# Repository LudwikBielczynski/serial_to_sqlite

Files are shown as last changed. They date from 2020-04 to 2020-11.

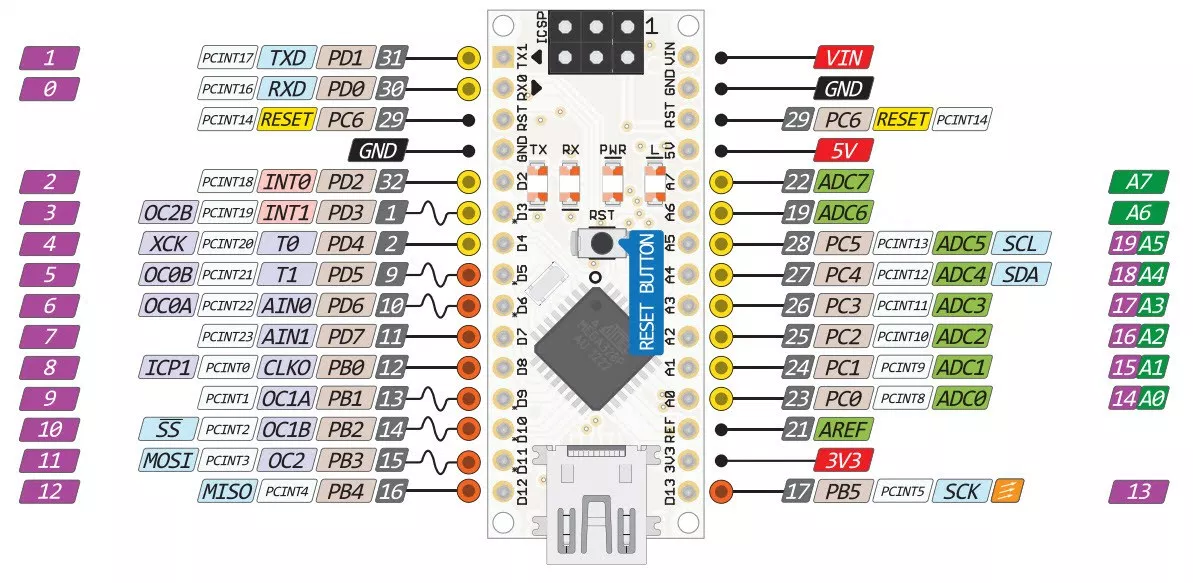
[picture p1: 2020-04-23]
schemes/arduino_nano_pin_layout.jpg

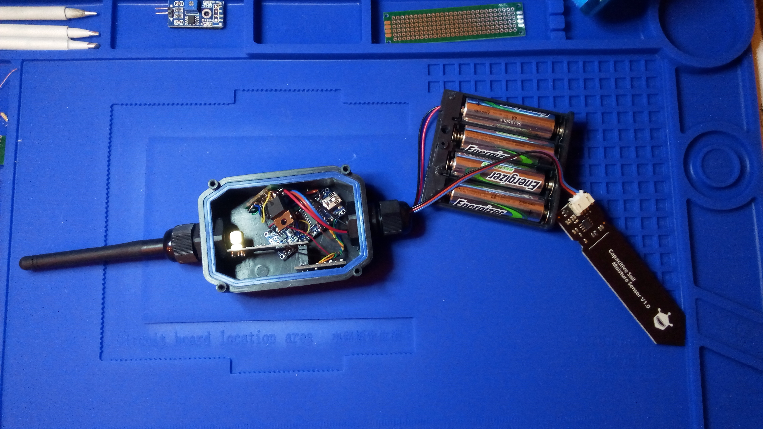
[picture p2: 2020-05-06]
prototypes/2020-05-06_soil_humidity_module.jpg

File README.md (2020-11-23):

# General scheme
General scheme of the watering control system is shown below:


Code to program transmitter and receiver arduino microcontrollers are available in sensors directory.

# Wiring schemes
## Receiver module
The wiring scheme for the receiver module is as follows:


## Soil humidity module
When compared with the receiver module, the wiring scheme of the soil humidity module has additionally (i) an external power supply, (ii) a voltage divider plugged to the analog pin (to measure the voltage of the battery), and (iii) the soil humidity sensor.


<!-- A prototype is shown below:
![alt text](https://github.com/LudwikBielczynski/watering_control_system/blob/master/prototypes/2020-05-06_soil_humidity_module.jpg) -->

# Receiver module
## Install as a service
The sensor_listener.service script should be placed in the /etc/systemd/system folder.

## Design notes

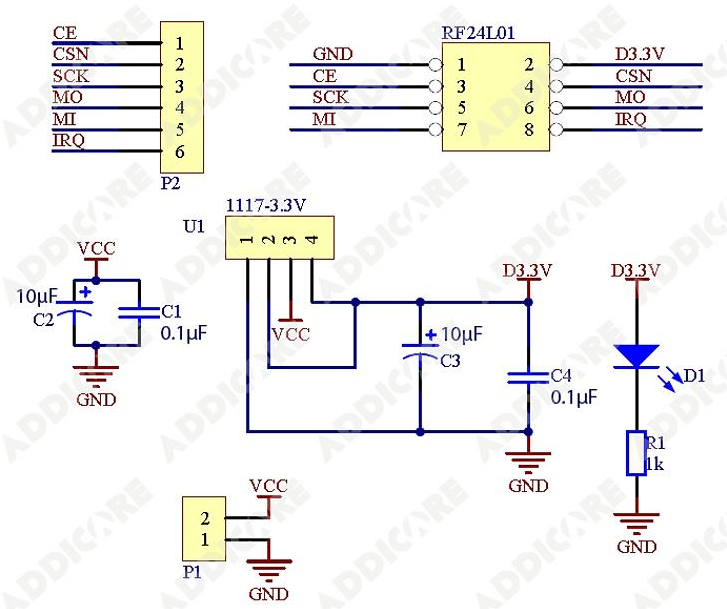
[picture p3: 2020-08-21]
technical_sheets/nRF24L01 socket adapter schematic.png

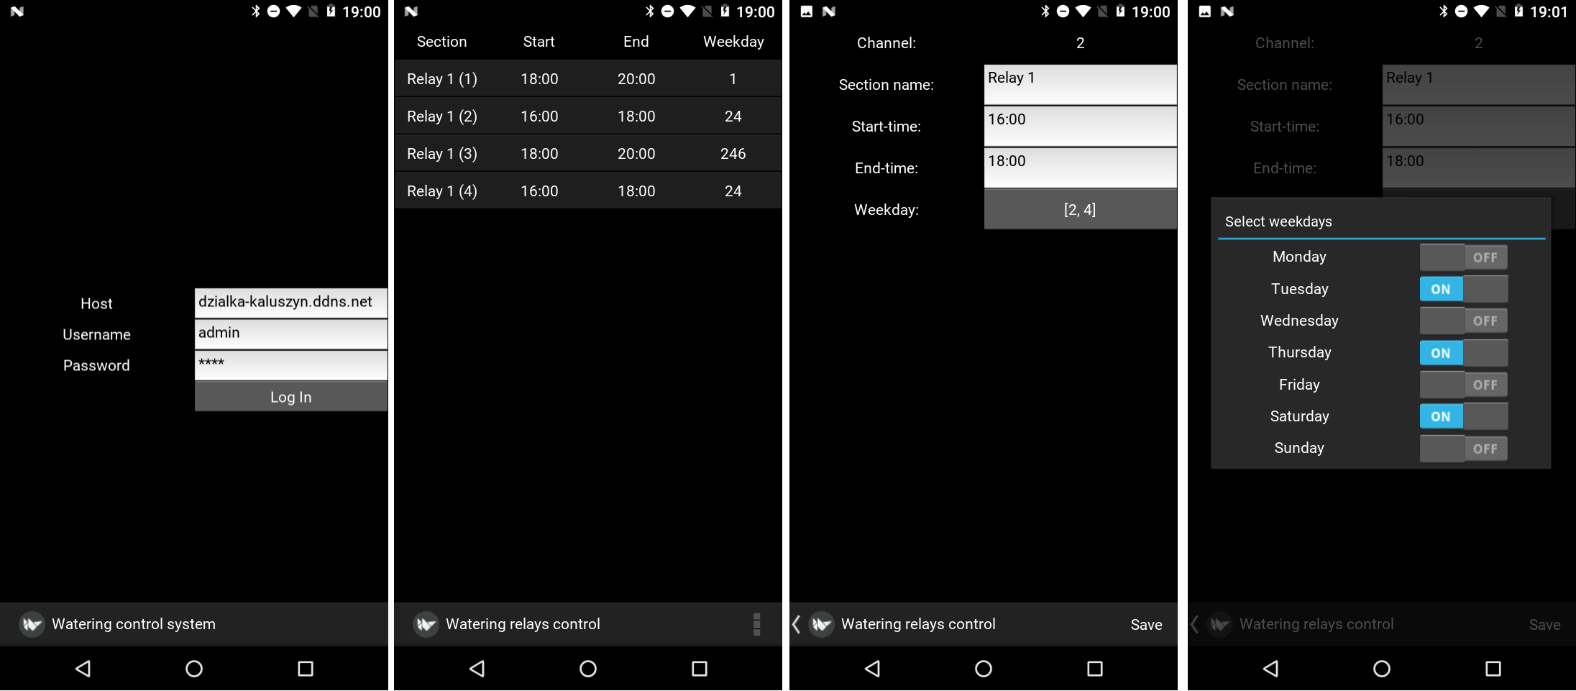
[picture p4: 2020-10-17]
android_app/android_app.png

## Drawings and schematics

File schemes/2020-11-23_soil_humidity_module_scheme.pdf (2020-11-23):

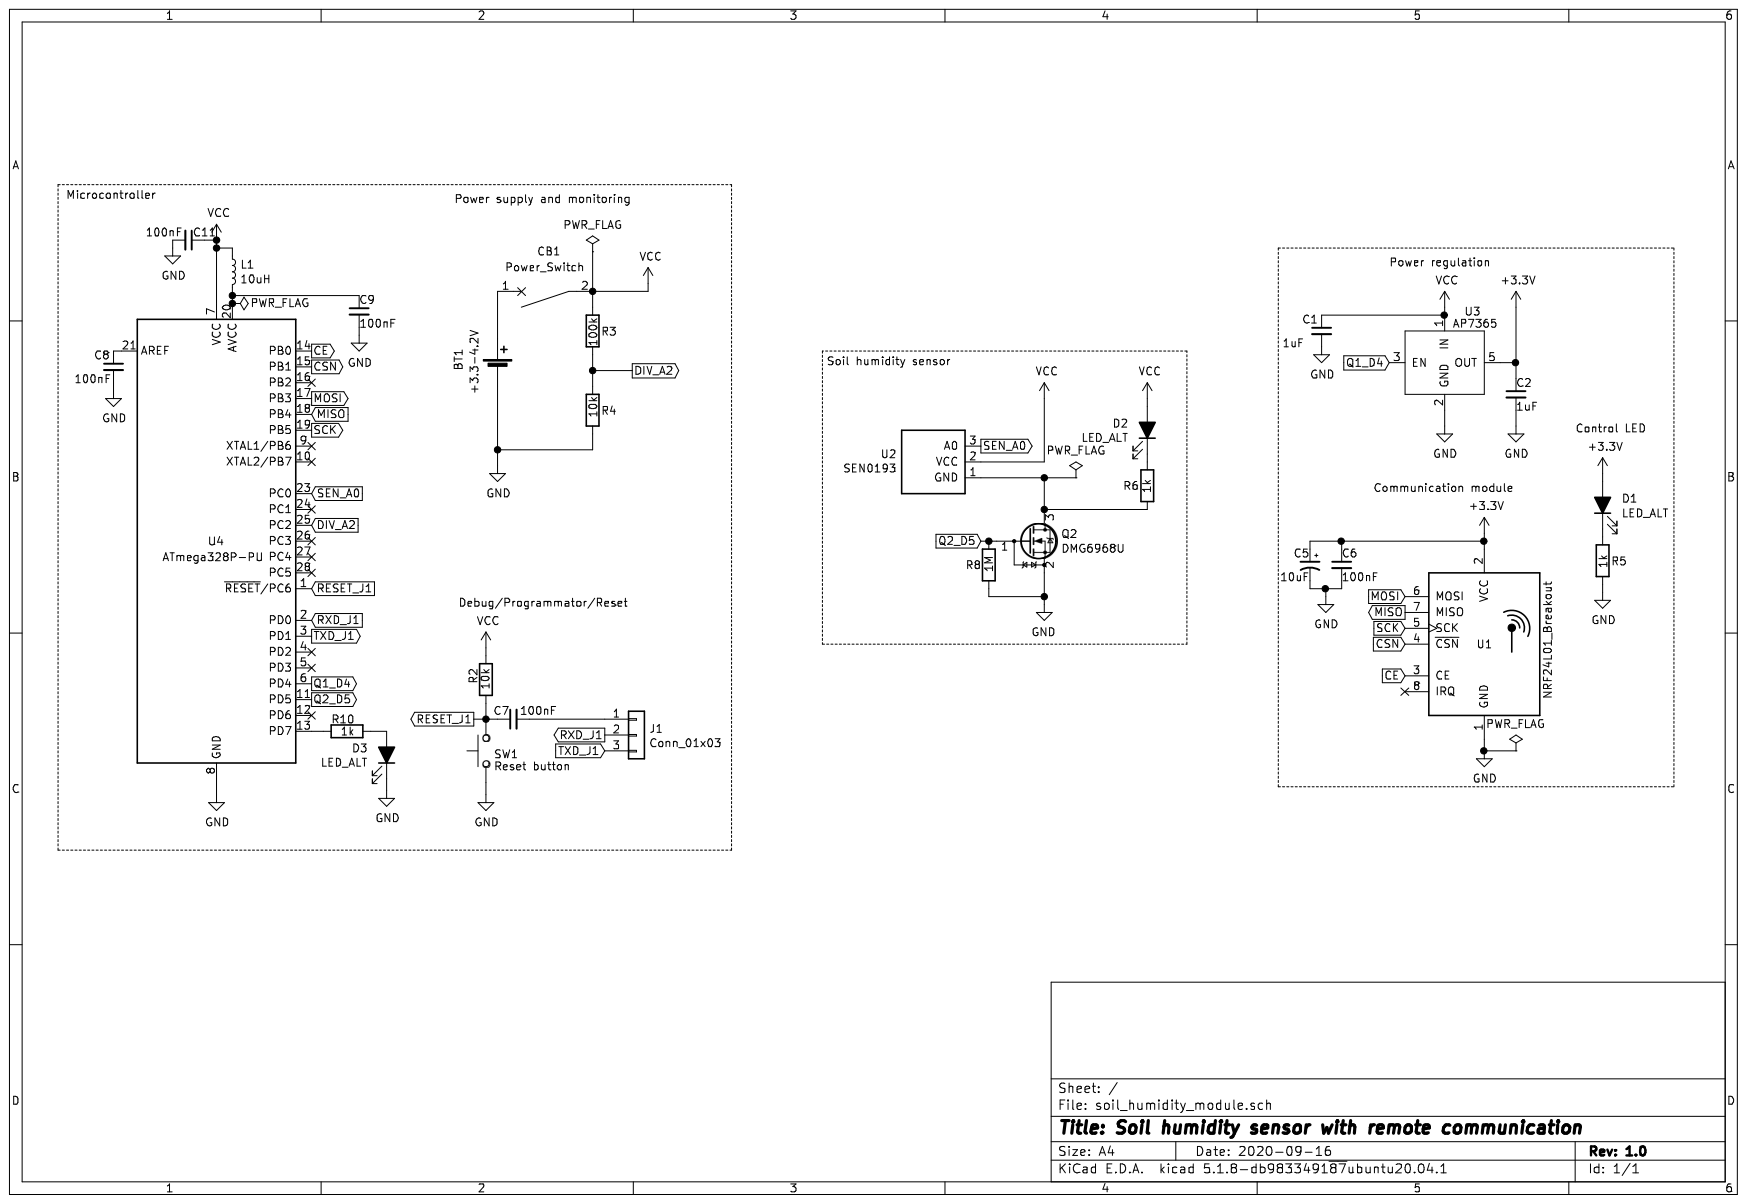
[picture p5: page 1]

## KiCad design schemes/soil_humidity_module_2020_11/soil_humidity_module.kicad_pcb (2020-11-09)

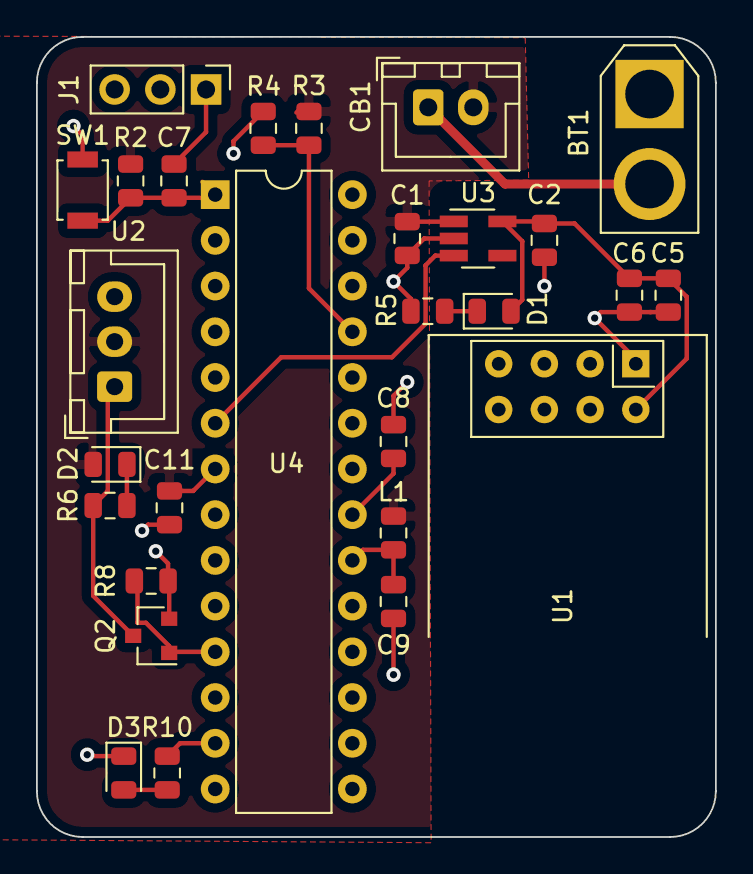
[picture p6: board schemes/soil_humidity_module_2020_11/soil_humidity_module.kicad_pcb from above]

Board: 4 copper layers, 37.7 x 44.5 mm, 28 parts (0 on the bottom side), 24 nets.

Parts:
BT1: +3.3-4.2V; AMASS_XT30U-F_1x02_P5.0mm_Vertical
C1, C2: 1uF; C_0805_2012Metric
C5: 10uF; C_0805_2012Metric
C6, C7, C8, C9, C11: 100nF; C_0805_2012Metric
CB1: Power_Switch; JST_XH_B2B-XH-A_1x02_P2.50mm_Vertical
D1, D2, D3: LED_ALT; LED_0805_2012Metric
J1: Conn_01x03; PinHeader_1x03_P2.54mm_Vertical
L1: 10uH; L_0805_2012Metric
Q2: DMG6968U; SOT-23
R2, R4: 10k; R_0805_2012Metric
R3: 100k; R_0805_2012Metric
R5, R6, R10: 1k; R_0805_2012Metric
R8: 1M; R_0805_2012Metric
SW1: Reset button; SW_SPST_B3U-1000P
U1: NRF24L01_Breakout; nRF24L01_PA_LNA_Breakout
U2: SEN0193; JST_XH_B3B-XH-A_1x03_P2.50mm_Vertical
U3: AP7365; SOT-23-5_HandSoldering
U4: ATmega328P-PU; DIP-28_W7.62mm

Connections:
+3V3: C2.1, C5.1, C6.1, D1.2, U1.2, U3.5
CE: U1.3, U4.14
CSN: U1.4, U4.15
DIV_A2: R3.2, R4.1, U4.25
GND: BT1.1, C1.2, C2.2, C5.2, C6.2, C8.2, C9.2, C11.2, D3.1, Q2.2, R4.2, R5.2, R8.2, SW1.1, U1.1, U3.2, U4.8, U4.22
MISO: U1.7, U4.18
MOSI: U1.6, U4.17
unnamed: BT1.2, CB1.1
unnamed: C7.2, J1.1
unnamed: C8.1, U4.21
unnamed: C9.1, L1.2, U4.20
unnamed: D1.1, R5.1
unnamed: D2.1, R6.1
unnamed: D3.2, R10.2
unnamed: Q2.3, R6.2, U2.1
unnamed: R10.1, U4.13
Q1_D4: U3.3, U4.6
Q2_D5: Q2.1, R8.1, U4.11
RESET_J1: C7.1, R2.1, SW1.2, U4.1
RXD_J1: J1.2, U4.2
SCK: U1.5, U4.19
SEN_A0: U2.3, U4.23
TXD_J1: J1.3, U4.3
VCC: C1.1, C11.1, CB1.2, D2.2, L1.1, R2.2, R3.1, U2.2, U3.1, U4.7

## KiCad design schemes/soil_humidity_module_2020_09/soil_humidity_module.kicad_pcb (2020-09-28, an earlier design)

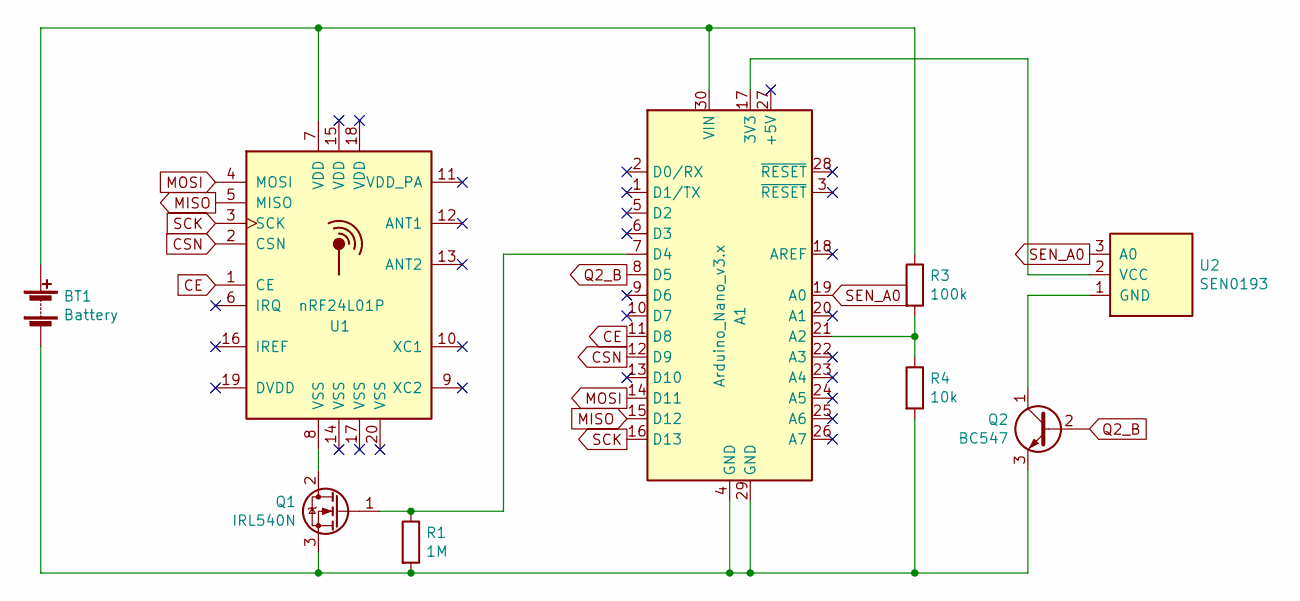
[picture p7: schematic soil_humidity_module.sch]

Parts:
A1: Arduino_Nano_v3.x; Arduino_Nano
BT1: Battery; AMASS_XT30U-F_1x02_P5.0mm_Vertical
Q1: IRL540N; TO-220-3_Vertical
Q2: BC547; TO-92_Inline
R1: 1M; R_0805_2012Metric_Pad1.15x1.40mm_HandSolder
R3: 100k; R_0805_2012Metric_Pad1.15x1.40mm_HandSolder
R4: 10k; R_0805_2012Metric_Pad1.15x1.40mm_HandSolder
U1: nRF24L01P; PinHeader_2x04_P2.54mm_Vertical
U2: SEN0193; JST_EH_B3B-EH-A_1x03_P2.50mm_Vertical

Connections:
CE: A1.11 (D8), U1.1 (CE)
CSN: A1.12 (D9), U1.2 (CSN)
MISO: A1.15 (D12), U1.5 (MISO)
MOSI: A1.14 (D11), U1.4 (MOSI)
unnamed: A1.7 (D4), Q1.1 (G), R1.1
unnamed: A1.17 (3V3), U2.2 (VCC)
unnamed: A1.21 (A2), R3.2, R4.1
unnamed: A1.4 (GND), A1.29 (GND), BT1.2 (-), Q1.3 (S), Q2.3 (E), R1.2, R4.2
unnamed: A1.30 (VIN), BT1.1 (+), R3.1, U1.7 (VDD)
unnamed: Q1.2 (D), U1.8 (VSS)
unnamed: Q2.1 (C), U2.1 (GND)
Q2_B: A1.8 (D5), Q2.2 (B)
SCK: A1.16 (D13), U1.3 (SCK)
SEN_A0: A1.19 (A0), U2.3 (A0)

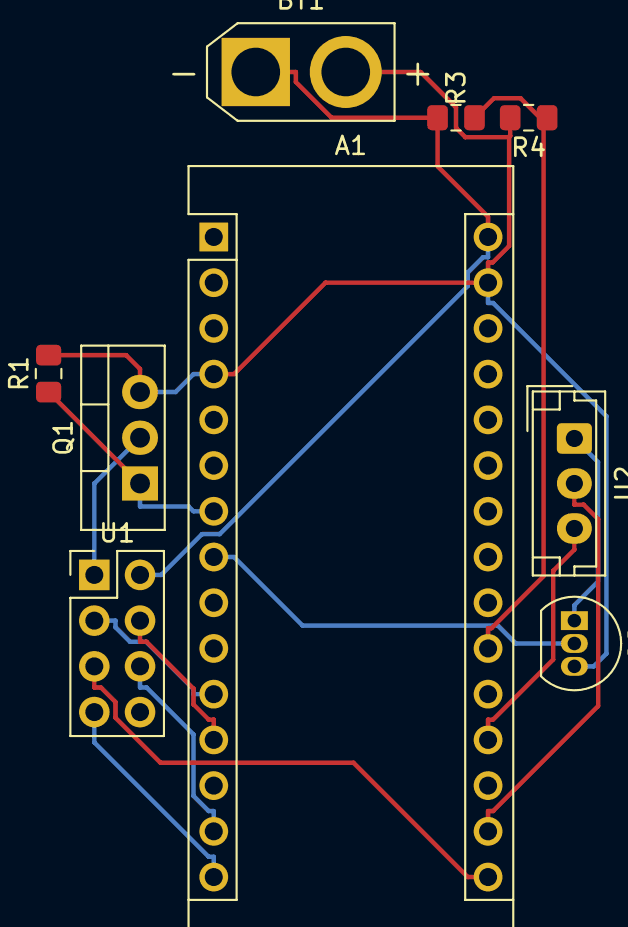
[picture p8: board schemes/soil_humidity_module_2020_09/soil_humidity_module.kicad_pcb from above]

Board: 2 copper layers, 9 parts (0 on the bottom side), 14 nets.

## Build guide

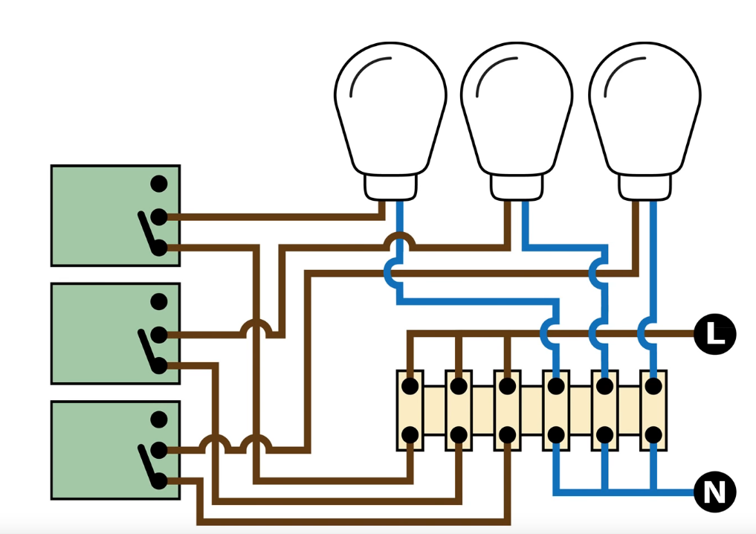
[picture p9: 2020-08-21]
schemes/Relay wiring example.png

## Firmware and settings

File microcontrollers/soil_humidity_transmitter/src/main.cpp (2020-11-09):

// the soil humidity sensor and the transmitter

#include "Transmitter.h"
#include "SoilHumiditySensor.h"
#include "Microcontroller.h"
#include <printf.h>

// Pin layout
const uint8_t MICROCONTROLLER_LED_ON_PIN = 7;
const uint8_t RADIO_POWER_PIN = 4;
const uint8_t SOIL_HUMIDITY_POWER_PIN = 5;
const uint8_t CE_PIN = 8;
const uint8_t CSN_PIN = 9;
const uint8_t SCK_PIN = 13; // default SCK pin
const uint8_t SOIL_HUMIDITY_SENSOR_PIN = 14; // A0
const uint8_t VOLTAGE_SPLITTER_PIN = 16; // A2

// Measure voltage settings
const unsigned short int VOLTAGE_MEASUREMENTS_NR = 10;
const float REFERENCE_VOLTAGE = 1.1;
const float VOLTAGE_SPLIT_FACTOR = 11.0; // based on (R1 + R2)/R2 where R1=100kOhm and R2=10kOhm
const float VOLTAGE_CORRECTION = 0.00;

// Soil humidity settings
const unsigned short int SOIL_MOISTURE_MEASUREMENTS_NR = 1;
int soilHumiditySensorValue;

// Transmitter settings
const uint64_t SLAVE_ADDRESS = 0xE6E6E6E6E6E6;
const unsigned short dataToSendSize = 12;

/****************************************************************************/

void setup() {
  Serial.begin(9600);
  Serial.println("Powered up the microprocessor...");
  pinMode(MICROCONTROLLER_LED_ON_PIN, OUTPUT);
  digitalWrite(MICROCONTROLLER_LED_ON_PIN, HIGH);

  // printf_begin();
  pinMode(RADIO_POWER_PIN, OUTPUT);
  pinMode(SOIL_HUMIDITY_POWER_PIN, OUTPUT);
}

/****************************************************************************/

void loop() {
  Serial.print("CPU frequency: ");
  Serial.println(F_CPU);
  delay(1000);

  // Read battery voltage before other components are powered up
  Microcontroller microcontroller(MICROCONTROLLER_LED_ON_PIN,
                                  VOLTAGE_SPLITTER_PIN,
                                  VOLTAGE_SPLIT_FACTOR,
                                  REFERENCE_VOLTAGE,
                                  VOLTAGE_CORRECTION);
  float voltage = 0;
  voltage = microcontroller.measureBatteryVoltage(VOLTAGE_MEASUREMENTS_NR);

  // Measure soil moisture
  SoilHumiditySensor soil_humidity_sensor(SOIL_HUMIDITY_POWER_PIN, SOIL_HUMIDITY_SENSOR_PIN);
  uint16_t soilHumiditySensorValue = 0;
  soilHumiditySensorValue = soil_humidity_sensor.measure(soilHumiditySensorValue, voltage);

  // Send data to the receiver
  Transmitter transmitter(CE_PIN, CSN_PIN, SCK_PIN, RADIO_POWER_PIN, SLAVE_ADDRESS);
  transmitter.turnOn();
  transmitter.setUp();

  char dataToSend[dataToSendSize] = ""; // Important to zero this variable before preparing data
  transmitter.prepareDataToSend(dataToSend, soilHumiditySensorValue, voltage);
  Serial.println(dataToSend);
  transmitter.sendData(dataToSend, dataToSendSize);

  transmitter.turnOff();

  microcontroller.sleep();

}

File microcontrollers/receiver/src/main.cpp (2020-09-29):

// SimpleRx - the slave or the receiver
// based on https://forum.arduino.cc/index.php?topic=421081
#include <Arduino.h>
#include <SPI.h>
#include <nRF24L01.h>
#include <RF24.h>

#include <printf.h>

#define CE_PIN 8
#define CSN_PIN 9

const uint64_t SLAVE_ADDRESS = 0xE6E6E6E6E6E6;

RF24 radio(CE_PIN, CSN_PIN);

void setup() {
  bool isSetupSuccess = false;

  Serial.begin(9600);
  printf_begin();
  Serial.println("Powered up the microprocessor...");

  isSetupSuccess = radio.begin();
  // Serial.print("Receiver initialization status: ");
  Serial.println(isSetupSuccess);
  // radio.printDetails();v
  Serial.println();

  if (isSetupSuccess) {
    // Set the pipe on the selected address address
    radio.openReadingPipe(1, SLAVE_ADDRESS);
    radio.setDataRate(RF24_250KBPS);
    radio.setPALevel(RF24_PA_MIN);
    radio.printDetails();

    // Set module as a receiver
    radio.startListening();
    Serial.println("Ready to receive. Listening...");
  }
  else
    Serial.println("There were issues during initial setup. The receiver is not ready.");
}


bool getData(char * dataReceived, unsigned short dataReceivedSize) {
  bool hasNewData = false;
  if (radio.available()) {
    radio.read(dataReceived, dataReceivedSize);
    hasNewData = true;
  }
  return hasNewData;
}


void showData(bool hasNewData, char * dataReceived) {
  if (hasNewData == true) {
    Serial.print("Rx=");
    Serial.println(dataReceived);
    hasNewData = false;
  }
}


void loop() {
  unsigned short dataReceivedSize = 12;
  char dataReceived[dataReceivedSize];
  bool hasNewData = false;

  hasNewData = getData(dataReceived, dataReceivedSize);
  showData(hasNewData, dataReceived);
}

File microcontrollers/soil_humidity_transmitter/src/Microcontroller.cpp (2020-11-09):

#include "Microcontroller.h"

void Microcontroller::discardFewFirstAnalogueReads(){
  for (size_t i = 0; i < 10; i++)
  {
    analogRead(voltage_splitter_pin);
    delay(10);
  }
}

/****************************************************************************/

float Microcontroller::measureBatteryVoltage(unsigned short int averaged_measurements_nr) {
  analogReference(INTERNAL);

  discardFewFirstAnalogueReads();

  int voltagesSum = 0;

  for (size_t i = 0; i < averaged_measurements_nr; i++)
  {
    voltagesSum += analogRead(voltage_splitter_pin);
    delay(10);
  }
  float voltage = voltage_split_factor * reference_voltage * voltagesSum / (1024.0 * averaged_measurements_nr) + voltage_correction;

  Serial.print("Voltage: ");
  Serial.print(voltage);
  Serial.println("V");
  return voltage;
}

/****************************************************************************/

const unsigned long SLEEP_INTERVAL_MS = 1;

void Microcontroller::sleep() {
  Serial.println("Starting to sleep");
  digitalWrite(microcontroller_led_on_pin, LOW);
  // delay(1000);

  sleep_enable();
  set_sleep_mode(SLEEP_MODE_PWR_SAVE); // Power-save mode disables BOD p.34

  clock_prescale_set(clock_div_128);
  // sleep_cpu();

  delay(50);
  // delay(10);
  clock_prescale_set(clock_div_1);
  power_all_enable();
  sleep_disable();

  Serial.println("Woke up");
  digitalWrite(microcontroller_led_on_pin, HIGH);
  delay(1000);
}

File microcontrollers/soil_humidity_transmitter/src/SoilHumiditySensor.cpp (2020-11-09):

#include "SoilHumiditySensor.h"

void SoilHumiditySensor::discardFewFirstAnalogueReads(){
  for (size_t i = 0; i < 10; i++)
  {
    analogRead(sensor_pin);
    delay(10);
  }
}

/****************************************************************************/

void SoilHumiditySensor::turnOn() {
  // Function used to turn on the soil humidity sensor
  digitalWrite(power_pin, HIGH);
  Serial.println("Turned on soil humidity sensor");
  delay(100);
}

/****************************************************************************/

void SoilHumiditySensor::turnOff() {
  // Function used to prepare everything and turn off soil humidity sensor
  digitalWrite(power_pin, LOW); // Power sensor down
  Serial.println("Turned off soil humidity sensor");
}

/****************************************************************************/

uint16_t SoilHumiditySensor::measure(uint16_t soilHumiditySensorValue,
                                     float batteryVoltage) {
  // Measured battery voltage will be used as the reference
  analogReference(DEFAULT);

  // functions used to return the value of the soil humidity from the sensor
  SoilHumiditySensor::turnOn();

  SoilHumiditySensor::discardFewFirstAnalogueReads();

  soilHumiditySensorValue = analogRead(sensor_pin);
  Serial.print("Soil humidity sensor value: ");
  Serial.print(soilHumiditySensorValue);
  Serial.print("; corrected: ");

  float voltageCorrection = batteryVoltage / _voltageOutputMax;
  Serial.print(soilHumiditySensorValue * voltageCorrection);
  Serial.print("; voltage correction: ");
  Serial.println(voltageCorrection);

  soilHumiditySensorValue = static_cast<int>(soilHumiditySensorValue * voltageCorrection);
  SoilHumiditySensor::turnOff();

  return soilHumiditySensorValue;
}

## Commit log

2020-03-14 Corrected names for the microcontrolers modules
    [main.cpp]
2020-03-14 Power down radio transmitter if not used
2020-03-15 Voltage measurements of the battery in the soil humidity transmitter
2020-03-15 Added receiver wiring scheme
2020-03-15 Soil humidity sensor scheme updated by the external power supply and the voltage divider
2020-04-13 Added transistor as a power switch for soil humidity sensor
2020-04-23 Updating scheme and ading a transistor as a power switch for the soild humidity sensor
2020-04-25 Add a sensor_listener.service and extend time between soil moisture measurements
2020-05-01 Added a transistor to switch on and off the radio in the transmitter
2020-05-01 Printing additional info in the transmitting module
2020-05-03 Using mosfet to power radio on the transmitter
2020-05-06 Added prototype picture
2020-07-26 Valve controller daemon api
2020-07-27 Valve controller API scaffold
2020-07-29 Expend front end for relay labels
2020-08-03 Updated scheme and extended the technical sheets
    [soil_humidity_module.kicad_pcb, soil_humidity_module.sch]
2020-08-09 Added weekdays selection popup. Changed front-end file structure
    [soil_humidity_module.sch]
2020-08-09 Weekdays pupup has activated switches reflecting relays state
2020-08-10 Singleton relays state is passed and modified between widgets
2020-08-17 Updated schemes and technical sheets
    [soil_humidity_module.sch]
2020-08-19 Improving soil humidity module scheme and pcb
    [soil_humidity_module.sch]
2020-08-21 Relay trials
2020-08-22 Correction to the channel relay setup
2020-08-22 Sensor listener moved to sensor_handler module
2020-08-22 [watering_starter] Setup relay board correctly
    [check_channels_on_relay_board.py, watering_starter.py]
2020-08-28 Updating relays state info
2020-08-28 [android_app] Added Clear and Send to host buttons
2020-08-28 [android_app] Handled timeout in case of host not available
2020-08-29 [watering_controller] Fixed route issue
    [watering_scheduler.py]
2020-08-29 [watering_controller] Fixed time check
    [watering_scheduler.py]
2020-09-13 [soil_huimidity_transmitter] Powering modules on and off working well
2020-09-28 [soil_huimidity_transmitter] Scheme improved. New PCB ordered
    [2020.09.26 Voltage divider with the internal Aref 32k resistor.ods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]
2020-10-03 [android_app] Relay controller implemented
2020-10-05 [android_app] Relay settings screen
2020-10-08 [android_app] Relay settings working
    [soil_humidity_module.dsn, soil_humidity_module.kicad_pcb, soil_humidity_module.sch]
2020-10-08 [android_app] Switches in weekdays popup is updating relays state on dismiss
2020-10-10 [soil_humidity_transmitter] Switching to internal 8MHz on ATMega
    [soil_humidity_module.kicad_pcb, soil_humidity_module.sch]
2020-10-18 [soil_humidity_transmitter] Using the watchdog to wake up the uC
    [soil_humidity_module-B_Cu.gbr, soil_humidity_module-B_Mask.gbr, soil_humidity_module-B_SilkS.gbr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]
2020-10-18 [android_app] During logging a data is fetched on a different thread
2020-11-02 [soil_humidity_transmitter] Simplification of the circuit
    [2020.09.26 Voltage divider with the internal Aref 32k resistor.ods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]
2020-11-09 [soil_humidity_transmitter] Voltage callibration of the sensor
    [2020.09.26 Voltage divider with the internal Aref 32k resistor.ods, 2020.11.07 Voltage callibration SoilHumiditySensor.ods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]
2020-11-09 [soil_humidity_transmitter] New version of the PCB
    [2020.09.26 Voltage divider with the internal Aref 32k resistor.ods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]
